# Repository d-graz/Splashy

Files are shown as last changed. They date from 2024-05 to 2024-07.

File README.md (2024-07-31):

# Splashy
<p align="center">
  
</p>

*"Splashy is a penguin shaped robot that helps you in refilling your water bottle"*
- Politecnico di Milan, Robotics \& Design course, A.Y. 2023/2024

<div align="center">
  <video src="https://github.com/user-attachments/assets/b8be0e26-66e1-40f9-9cfe-064658929ba2" width="1280" />
</div>

### Table of content
- [Introduction](#introduction)
- [Do It Yourself](#diy)
- [Credits](#credits)

## Introduction
This project started with the task *to create something that would have changed the behavior of people* (for the better of course =) ) on campus, given the constrain of non-mobility of such robot. Given such a constrain we explored some ideas before realizing that plastic has been a problem since forever and that the water refillers on campus where not that good. In fact thoose machines were slow resulting in a booring queue during peak hours. This somethimes would result in people buying  plastic water bottles from vending machines.\
Now i will **briefly** present some design challenges encoutered during developing of such a project. The full report can be found [here](documentation/report.pdf)

### How to attract people the first time (discovery)
The robot embeds a `PIR Sensor` able to detect motion. If the robot is not current under usage it will attract people passing by using it's wings (`servo motors` handles motion) and adjusting it's facial expression(rendered using `8x8 led matrices`).

### How to attract people in the long run (re-usage)
Splashy has a `NFC Reader`. This nfc can be used to identify users and thus create a rank based on the quantity of recharges that have been made. The rank is presented using an `LCD Screen`. This creates a gamification aspect in the refilling process

### Distribution of water
The water can be pumped from a water tank using a `pump` (like in our case) or alternative the penguin can be directly attached to a pressured faucet by replacing the pump with a `electric driven valve` 

## DIY
If you plan to recreate this project:
1. find all the components used for Splasy [here](documentation/BOM.pdf)
2. find all the 3d-printable in the `stl` directory
3. give a **careful** read to the [report](documentation/report.pdf)
4. Additionally read [user manual](documentation/user_manual.pdf) and [maintence manual](documentation/maintence_manual.pdf)

## Credits
<p align="center">
  
</p>

From left to rigth:
- Gianluca Miglietta (Automation Engineer)
- Davide Grazzani    (me, Computer Science Engineer)
- Sofia Maria Ciccia (School of Design and Engineering)
- Enrico Virgili     (School of Design and Engineering)

Supervisors:
- prof. Andrea Bonarini
- prof. Maximiliano Ernesto Romero

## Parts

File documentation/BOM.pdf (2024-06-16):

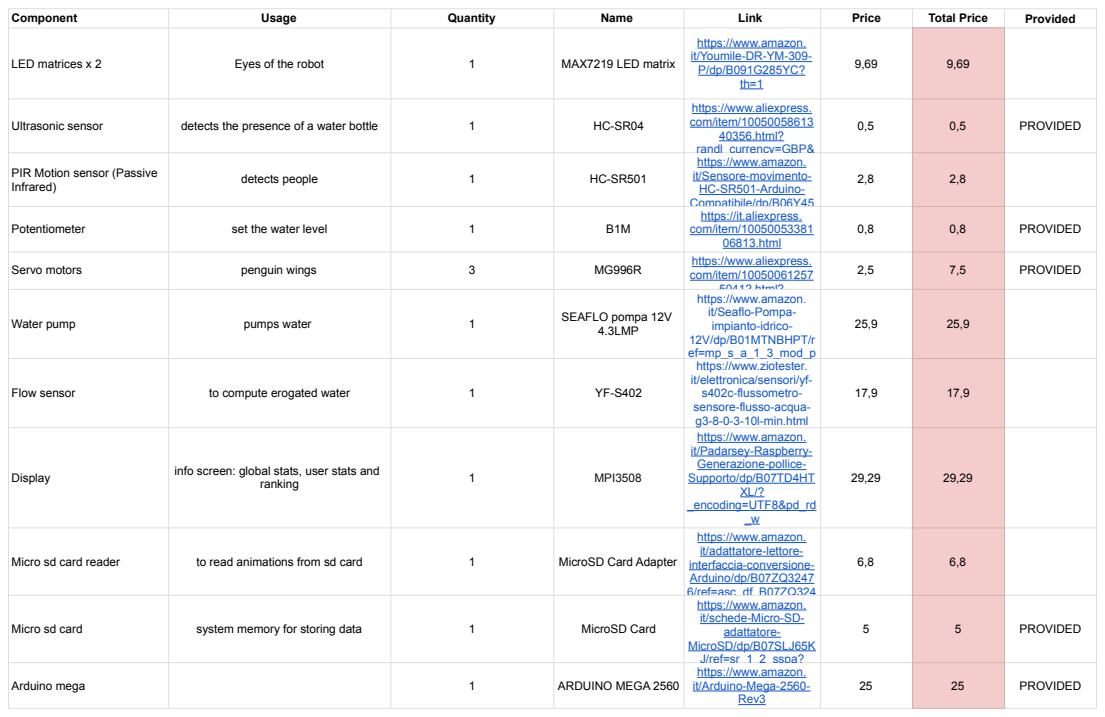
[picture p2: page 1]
Component; Usage; Quantity; Name; Link; Price; Total Price; Provided; LED matrices x 2; Eyes of the robot; MAX7219 LED matrix; Ultrasonic sensor; detects the presence of a water bottle; PROVIDED; Infrared); detects people; Potentiometer; set the water level; Servo motors; penguin wings; Water pump; pumps water; SEAFLO pompa 12V 4.3LMP; Flow sensor; to compute erogated water; Display; info screen: global stats, user stats and; ranking; MPI3508; Micro sd card reader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

https://www.amazon.
it/Youmile-DR-YM-309-

https://www.aliexpress.
com/item/10050058613
40356.html?
_randl_currency=GBP& (https://www.aliexpress.com/item/1005005861340356.html?_randl_currency=GBP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)
it/Sensore-movimento-
HC-SR501-Arduino-
Compatibile/dp/B06Y45 (https://www.amazon.it/Sensore-movimento-HC-SR501-Arduino-Compatibile/dp/B06Y459ZZK)
https://it.aliexpress.
com/item/10050053381
06813.html (https://it.aliexpress.com/item/1005005338106813.html?src=google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)
com/item/10050061257 (https://www.aliexpress.com/item/1005006125750412.html?src=google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)
50412.html?
it/Seaflo-Pompa-
impianto-idrico-
12V/dp/B01MTNBHPT/r
ef=mp_s_a_1_3_mod_p (https://www.amazon.it/Seaflo-Pompa-impianto-idrico-12V/dp/B01MTNBHPT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)
https://www.ziotester.
it/elettronica/sensori/yf-
s402c-flussometro-
sensore-flusso-acqua-
g3-8-0-3-10l-min.html (https://www.ziotester.it/elettronica/sensori/yf-s402c-flussometro-sensore-flusso-acqua-g3-8-0-3-10l-min.html)

PIR Motion sensor (Passive

https://www.amazon.it/Padarsey-Raspberry-Generazione-pollice-Supporto/dp/B07TD4HT 29,29 XL/? _encoding=UTF8&pd_rd _w (https://www.amazon.it/Padarsey-Raspberry-Generazione-pollice-Supporto/dp/B07TD4HTXL/) | 29,29

https://www.amazon.it/adattatore-lettore-interfaccia-conversione-6,8Arduino/dp/B07ZQ32476/ref=asc_df_B07ZQ324 (https://www.amazon.it/adattatore-lettore-interfaccia-conversione-Arduino/dp/B07ZQ32476?hvadid=655703548252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) https://www.amazon.it/schede-Micro-SD-adattatore-5MicroSD/dp/B07SLJ65KJ/ref=sr_1_2_sspa? (https://www.amazon.it/schede-Micro-SD-adattatore-MicroSD/dp/B07SLJ65KJ?sp_csd=d2lkZ2V0TmFtZT1zcF9hdGY) https://www.amazon.it/Arduino-Mega-2560-25 Rev3 (https://www.amazon.it/Arduino-Mega-2560-Rev3-microcontrollore/dp/B0046AMGW0?hvadid=194963093038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) | | 6,8 5 25 | PROVIDED

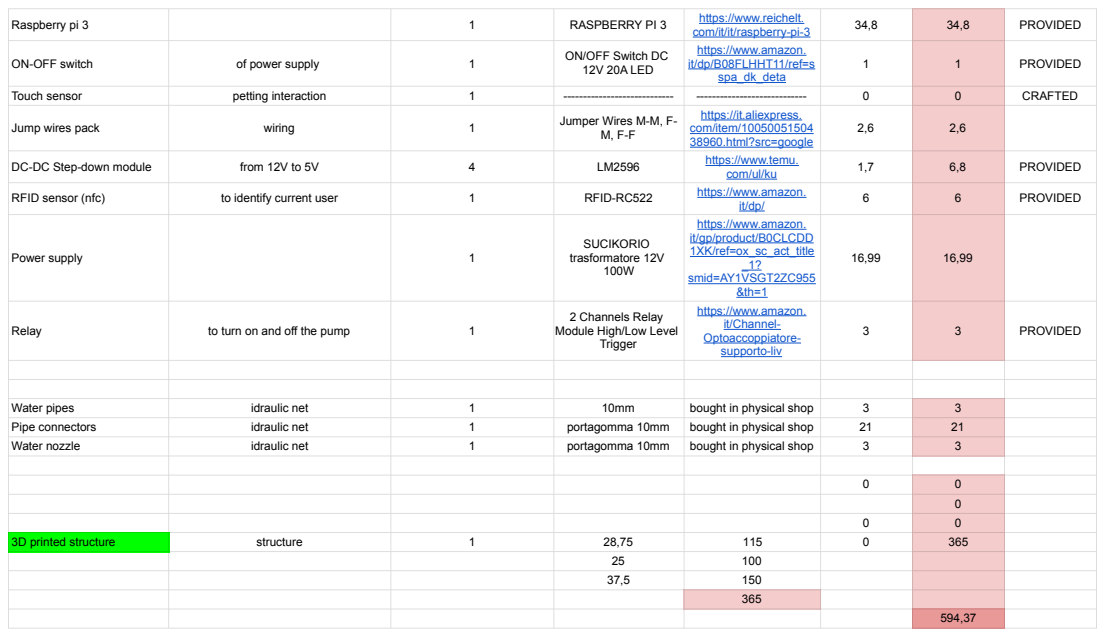
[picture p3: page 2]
Raspberry pi 3; RASPBERRY PI 3; https://www.reichelt.; com/it/it/raspberry-pi-3; PROVIDED; ON-OFF switch; of power supply; ON/OFF Switch DC; 12V 20A LED; Touch sensor; petting interaction; CRAFTED; Jump wires pack; wiring; Jumper Wires M-M, F- M, F-F; DC-DC Step-down module; from 12V to 5V; https://www.temu.; com/ul/ku; RFID sensor (nfc); to identify current user; RFID-RC522; https://www.amazon.; Power supply; SUCIKORIO trasformatore 12V 100W; _1? smid=AY1VSGT2ZC955 &th=1; Relay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

https://www.amazon.
it/dp/B08FLHHT11/ref=s
spa_dk_deta (https://www.amazon.it/dp/B08FLHHT11?s=industrial&sp_csd=d2lkZ2V0TmFtZT1zcF9kZXRhaWw)

https://it.aliexpress.
com/item/10050051504
38960.html?src=google (https://it.aliexpress.com/item/1005005150438960.html?src=google)

it/gp/product/B0CLCDD
1XK/ref=ox_sc_act_title

it/Channel-
Optoaccoppiatore-
supporto-liv (https://www.amazon.it/Channel-Optoaccoppiatore-supporto-livello-attivazione/dp/B07QLX1YZN)

2 Channels Relay
Module High/Low Level

3D printed structure | structure 1 28,75 115 0 | 365

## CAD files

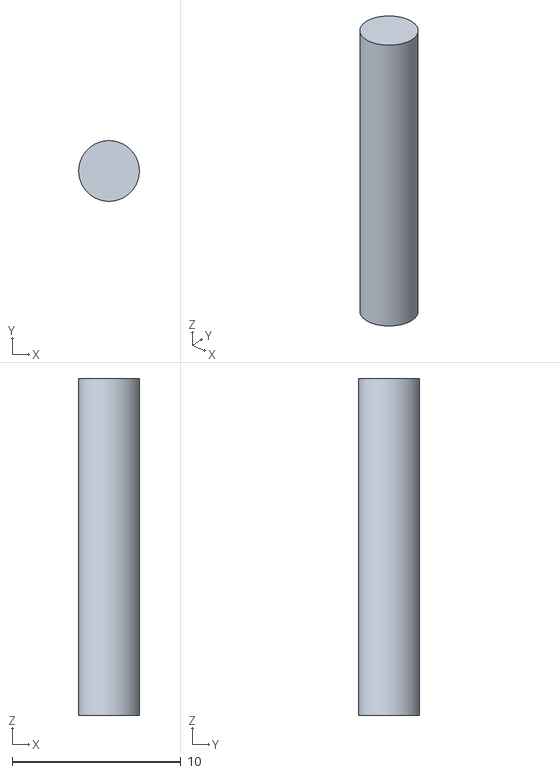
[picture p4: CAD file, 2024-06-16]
stl/wing_center_joint_x2.STL
3.60 x 3.60 x 20.0

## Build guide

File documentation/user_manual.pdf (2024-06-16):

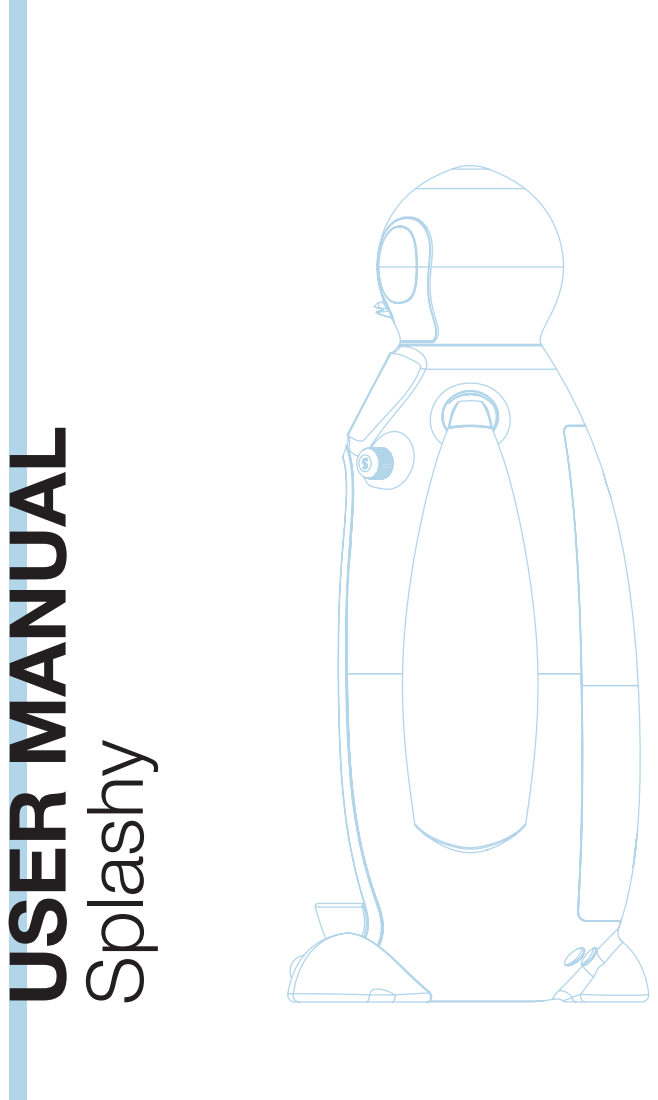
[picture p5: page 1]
pla

# DESIGN&ROBOTICS

## Professors:

## Andrea Bonarini, Maximiliano Romero

## Tutors:

## Federico Espositi

## Group 3

## Sofia Maria Ciccia Davide Grazzani Gianluca Miglietta Enrico Virgili

## 12° edition, 2024

# INDEX

1234

## introduction

## how to start

## how to use

## emotions

# 1introduction

## who is Splashy?

Splashy: Refill your Water Bottle,

## Refresh the Planet!

Splashy is an innovative water dispenser,

designed to be usable by anyone in many contexts, but with a strong sustainable objective. The idea of Splashy was born from the need to change an incorrect and harmful behavior for the environment: the continuous use of plastic bottles. This behavior contributes significantly to our planet's CO2 footprint. Splashy wants to encourage you to constantly use the water bottle, thus performing a positive action for the environment, making the experience

more engaging and pleasant than usual.

## Thanks to its intuitive and attractive interface, its attractive design and integrated gamification elements, Splashy incentivizes you to come back and use the service. Automatic and super-fast refilling of your water bottle makes Splashy not only a sustainable option, but also

convenient and fun.

## head

## LED screen

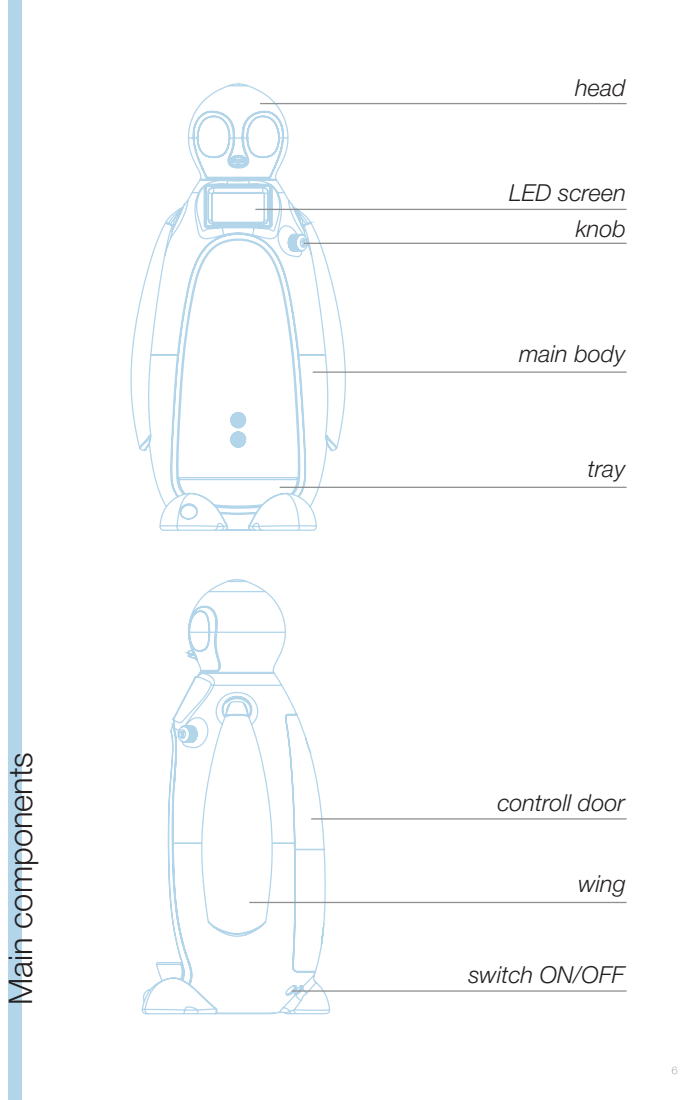
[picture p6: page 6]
Main components; knob; main body; tray; controll door; wing

switch ON/OFF

# 2how to start

1
2

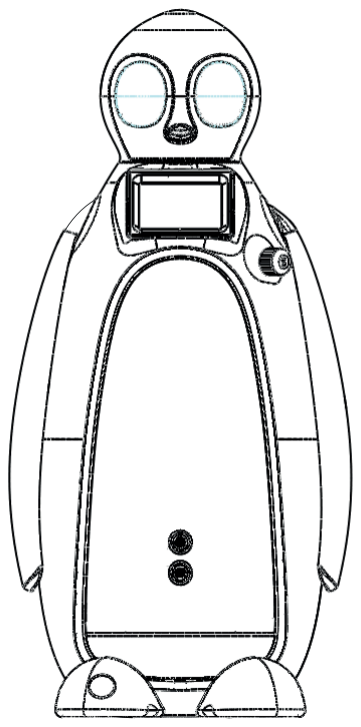
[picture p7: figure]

1

Take from the box Splashy. The robot doesn’t need any kind of assembly. You can start to use immediately!
Place the robot on a stable surface.

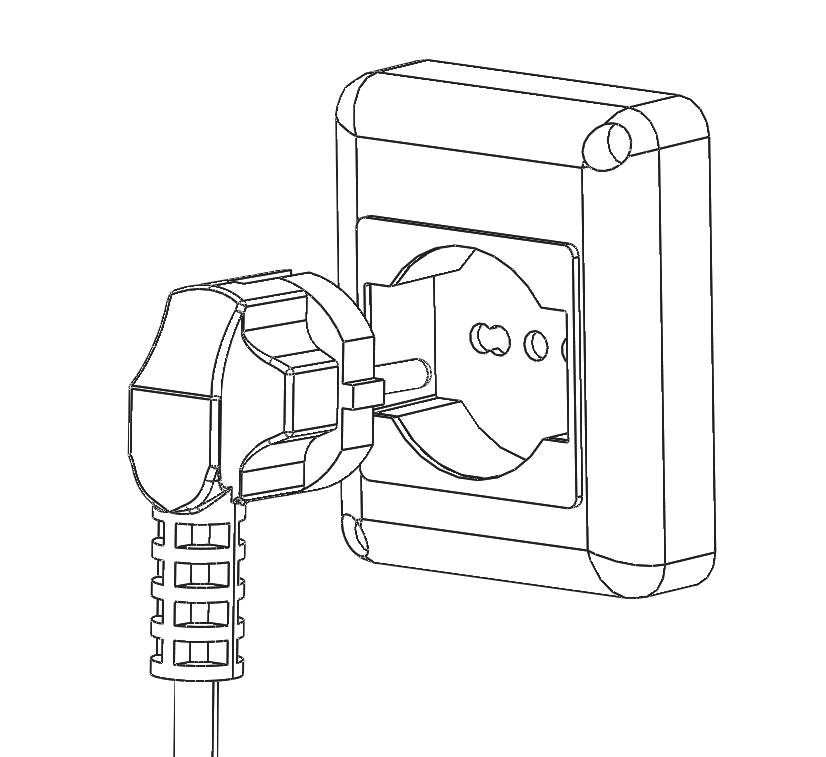
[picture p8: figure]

2

Plug the Schuko cable into the electric socket.

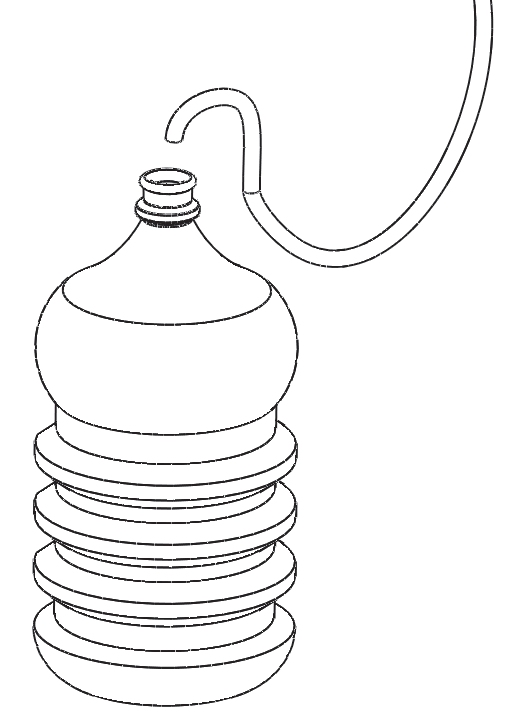
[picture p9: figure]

3

Put the water pipe into the gallon.

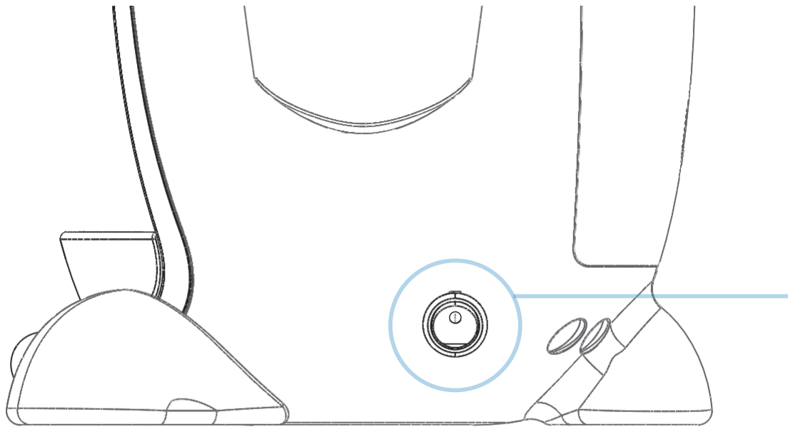
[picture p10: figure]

4

Turn on the robot from the switch

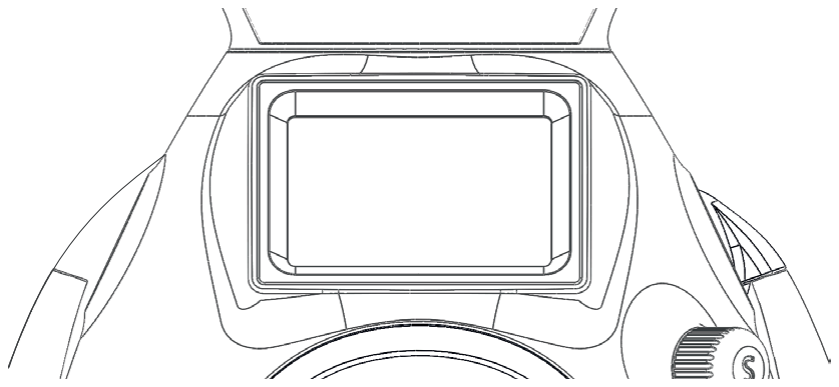
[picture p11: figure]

5

Wait until the screen shows the ranking

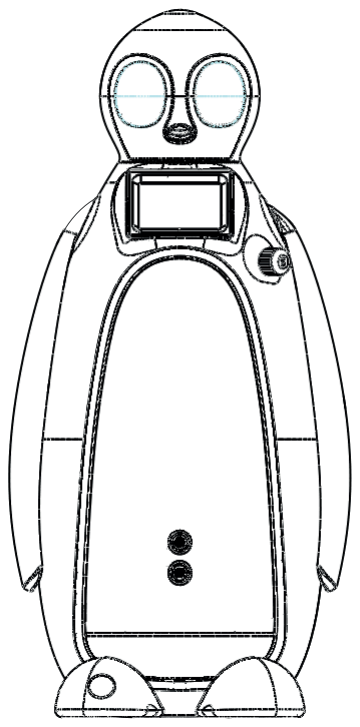
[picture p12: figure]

6

Now you can freely use the robot!

# 3how to use

2

1

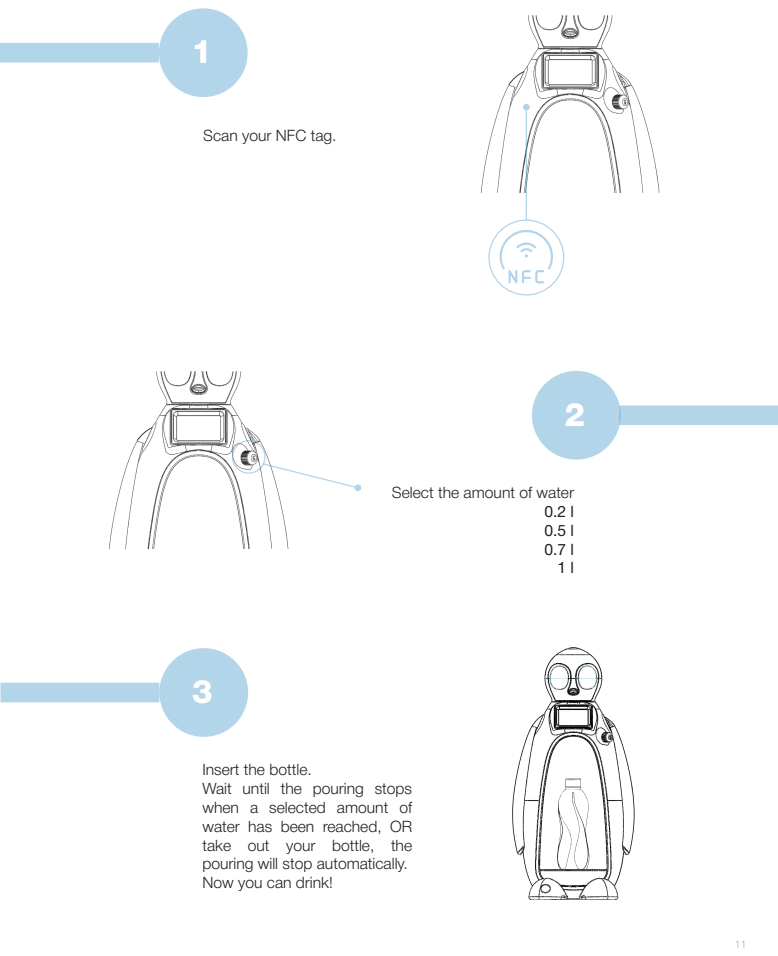
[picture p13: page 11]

Scan your NFC tag.

Select the amount of water

Insert the bottle.
Wait until the pouring stops
when a selected amount of
water has been reached, OR
take out your bottle, the
pouring will stop automatically.
Now you can drink!

2

# 4emotions

1

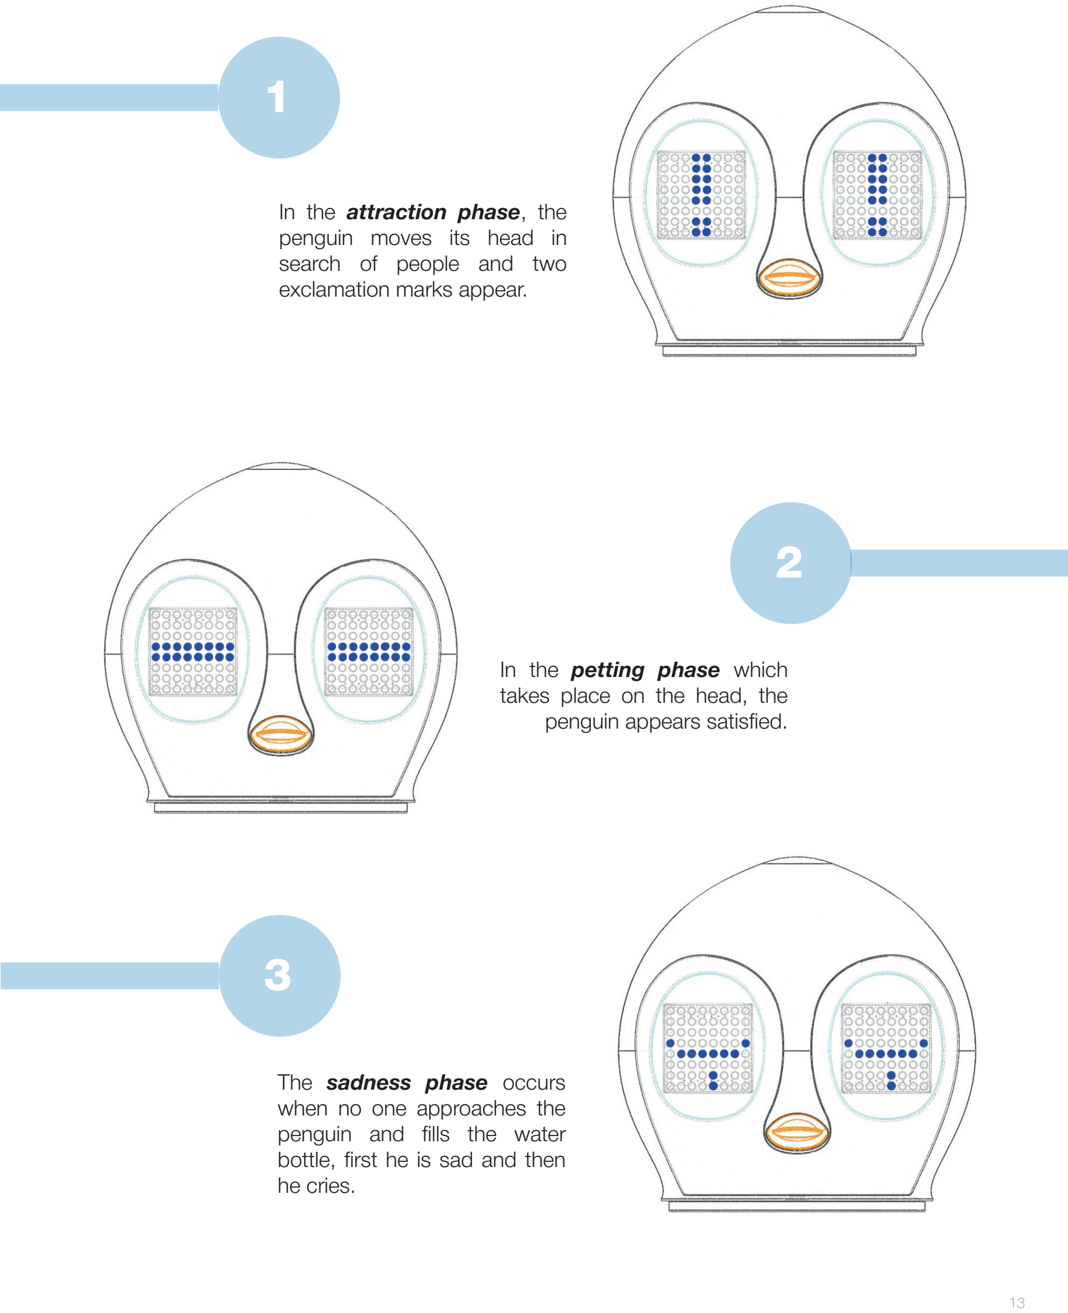
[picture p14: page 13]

In the attraction phase, the penguin moves its head in
search of people and two
exclamation marks appear.

2

In the petting phase which takes place on the head, the penguin appears satisfied.

3

The sadness phase occurs
when no one approaches the penguin and fills the water bottle, first he is sad and then he cries.

3

4

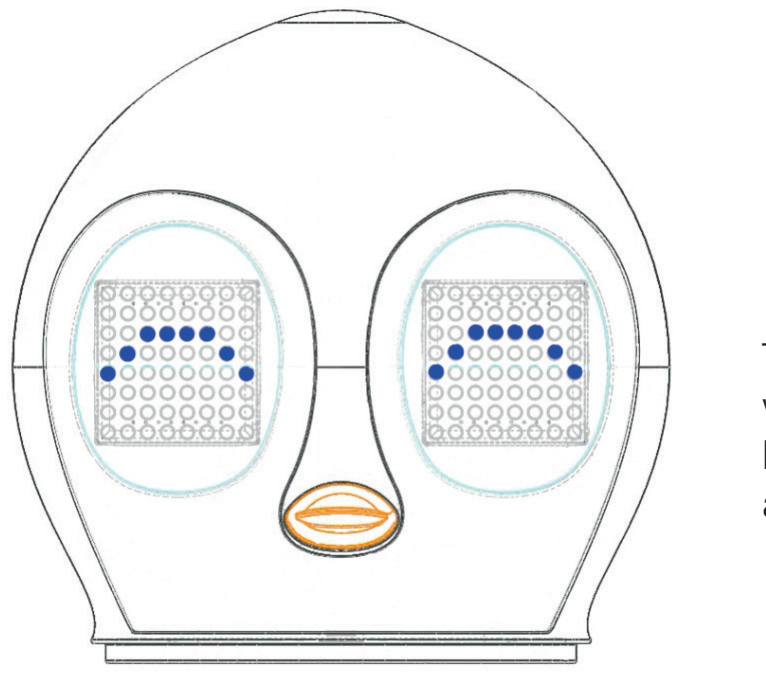
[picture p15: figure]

The happiness phase occurs when someone fills the water
bottle, | when | someone
approaches and after every 5
| | bottles filled

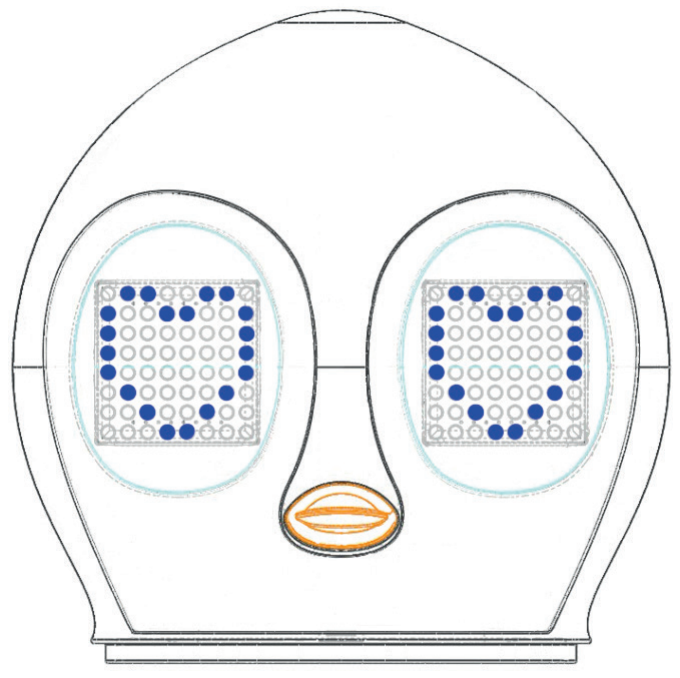
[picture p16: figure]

5

During the water refill phase, the eyes become two hearts that fill gradually, until they are completely full when they flash and it is possible to remove the bottle

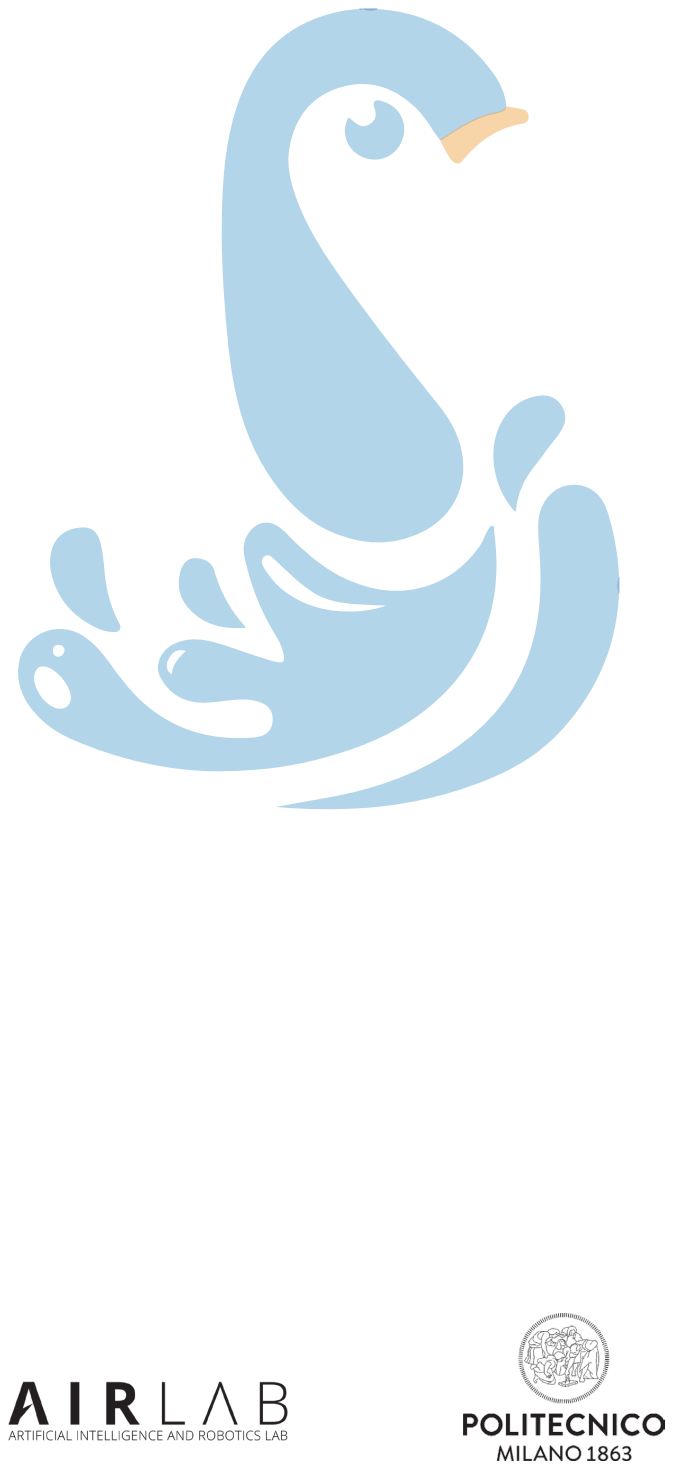
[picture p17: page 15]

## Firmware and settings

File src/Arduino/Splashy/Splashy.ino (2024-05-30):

// ####################### LIBRARIES ###########################
// release libraries
#include "libraries/Config/Config.hpp"


//#define DEBUG
//#define WARN
//#define TEST 
// debug libraries
#include "libraries/LedMatrix/LedMatrix.hpp"
#include "libraries/LedMatrix/LedMatrix.cpp"
#include "libraries/MySD/MySD.hpp"
#include "libraries/MySD/MySD.cpp"
#include "libraries/TaskManagement/TaskManagement.hpp"
#include "libraries/TaskManagement/TaskManagement.cpp"
#include "libraries/ServoController/ServoController.hpp"
#include "libraries/ServoController/ServoController.cpp"
#include "libraries/UltrasonicSensor/UltrasonicSensor.hpp"
#include "libraries/UltrasonicSensor/UltrasonicSensor.cpp"
#include "libraries/ProximitySensor/ProximitySensor.hpp"
#include "libraries/ProximitySensor/ProximitySensor.cpp"
#include "libraries/FiniteStateMachine/FiniteStateMachine.hpp"
#include "libraries/FiniteStateMachine/FiniteStateMachine.cpp"
#include "libraries/Pump/Pump.hpp"
#include "libraries/Pump/Pump.cpp"
#include "libraries/TouchSensor/TouchSensor.hpp"
#include "libraries/TouchSensor/TouchSensor.cpp"
#include "libraries/Config/Global.hpp"
#include "libraries/Core/Core.hpp"
#include "libraries/Core/Core.cpp"


// ######################## DEFINE #############################
#define BAUD_RATE 9600

// ##################### GLOBAL VARS ###########################
// scheduler
Scheduler *scheduler;

// fsm
FiniteStateMachine *fsm;


// ##################### SETUP #################################
void setup() {
  // start serial communication
  Serial.begin(BAUD_RATE);
  delay(2000);
  #ifdef DEBUG
    Serial.println(F("Init setup"));
    #ifdef TEST
      delay(1000);
    #endif
  #endif

  //init the scheduler
  scheduler = new Scheduler();

  //init the led matrix early to enable error handling
  #ifdef DEBUG
    Serial.println(F("Init LedMatrix"));
  #endif
  led_matrix = new LedMatrix("Led");
  handle_error(scheduler->add_task(led_matrix), F("Failed to add LedMatrix to the scheduler"));

  //init the sd card early to load boot animation
  #ifdef DEBUG
    #ifdef TEST
      delay(1000);
    #endif
    Serial.println(F("Init SD card"));
  #endif
  handle_error(init_sd(), F("Failed to initialize SD card"));

  //load the boot animation
  #ifdef DEBUG
    #ifdef TEST
      delay(1000);
    #endif
    Serial.println(F("Loading boot animation"));
  #endif
  handle_error(led_matrix->load_animation(LedMatrixAnimation::Boot), F("Failed to load boot animation"));
  handle_error(scheduler->executeByName(F("Led"), 3), F("Failed to execute LedMatrix"));

  //init the servo controller
  #ifdef DEBUG
    #ifdef TEST
      delay(1000);
    #endif
    Serial.println(F("Init ServoController, adding to the scehduler and homing the servo"));
  #endif
  servo_controller = new ServoController("Servo");
  handle_error(scheduler->add_task(servo_controller), F("Failed to add ServoController to the scheduler"));
  handle_error(scheduler->executeByName(F("Led")), F("Failed to execute LedMatrix"));
  servo_controller->home(true);
  handle_error(scheduler->executeByName(F("Led"), 3), F("Failed to execute LedMatrix"));

  //testing servo motors if test
  #ifdef DEBUG
    #ifdef TEST
      Serial.println(F("Testing servo motors"));
      handle_error(servo_controller->load_animation(ServoMotorAnimation::Test), F("Failed to load test animation for servocontroller"));
      while(servo_controller->get_status() != TaskStatus::HIBERNATED){
        handle_error(scheduler->executeAll(), F("Failed to execute the scheduler"));
      }
      Serial.println(F("Test done"));
      Serial.println(F("Continuing the boot process"));
    #endif
  #endif

  //init the ultrasonic sensor
  #ifdef DEBUG
    #ifdef TEST
      delay(1000);
    #endif
    Serial.println(F("Init UltrasonicSensor and adding to the scheduler"));
  #endif
  ultrasonic_sensor = new UltrasonicSensor("Usonic");
  handle_error(scheduler->executeByName(F("Led")), F("Failed to execute LedMatrix"));
  handle_error(scheduler->add_task(ultrasonic_sensor), F("Failed to add UltrasonicSensor to the scheduler"));
  handle_error(scheduler->executeByName(F("Led"), 3), F("Failed to execute LedMatrix"));

  //init the proximity sensor
  #ifdef DEBUG
    #ifdef TEST
      delay(1000);
    #endif
    Serial.println(F("Init ProximitySensor and adding to the scheduler"));
  #endif
  proximity_sensor = new ProximitySensor("Prox");
  handle_error(scheduler->executeByName(F("Led")), F("Failed to execute LedMatrix"));
  handle_error(scheduler->add_task(proximity_sensor), F("Failed to add ProximitySensor to the scheduler"));
  handle_error(scheduler->executeByName(F("Led"), 3), F("Failed to execute LedMatrix"));

  //init the pump
  #ifdef DEBUG
    #ifdef TEST
      delay(1000);
    #endif
    Serial.println(F("Init Pump and adding to the scheduler"));
  #endif
  pump = new Pump("Pump");
  handle_error(scheduler->executeByName(F("Led")), F("Failed to execute LedMatrix"));
  handle_error(scheduler->add_task(pump), F("Failed to add Pump to the scheduler"));
  handle_error(scheduler->executeByName(F("Led")), F("Failed to execute LedMatrix"));

  //init the touch sensor
  #ifdef DEBUG
    #ifdef TEST
      delay(1000);
    #endif
    Serial.println(F("Init TouchSensor and adding to the scheduler"));
  #endif
  touch_sensor = new TouchSensor("Touch");
  //handle_error(scheduler->executeByName(F("Led")), F("Failed to execute LedMatrix"));
  //handle_error(scheduler->add_task(touch_sensor), F("Failed to add TouchSensor to the scheduler"));
  //handle_error(scheduler->executeByName(F("Led"), 3), F("Failed to execute LedMatrix"));

  //init the fsm
  #ifdef DEBUG
    #ifdef TEST
      delay(1000);
    #endif
    Serial.println(F("Init FiniteStateMachine"));
  #endif
  fsm = new FiniteStateMachine();
  handle_error(scheduler->executeByName(F("Led"), 2), F("Failed to execute LedMatrix"));

  // activating proximity sensor, ultrasonic sensor and proximity before entering the loop in IDLE status
  #ifdef DEBUG
    #ifdef TEST
      delay(1000);
    #endif
    Serial.println(F("Activating proximity sensor and ultrasonic sensor before entering the loop in IDLE status"));
  #endif
  handle_error(proximity_sensor->activate(), F("Failed to activate proximity sensor"));
  handle_error(ultrasonic_sensor->activate(), F("Failed to activate ultrasonic sensor"));
  handle_error(touch_sensor->activate(), F("Failed to activate touch sensor"));
  handle_error(scheduler->executeByName(F("Led"), 3), F("Failed to execute LedMatrix"));

  //load the idle animation facial expression
  handle_error(led_matrix->load_animation(LedMatrixAnimation::Idle), F("Failed to load idle animation"));

  #ifdef DEBUG
    Serial.println(F("Setup done"));
    #ifdef TEST
      delay(1000);
    #endif
  #endif

}


// ######################## LOOP ###############################
void loop() {
  // execute the fsm
  #ifdef DEBUG
    #ifdef WARN
      Serial.println(F("Executing the FSM"));
    #endif
  #endif
  fsm->next();

  // execute the scheduler
  #ifdef DEBUG
    #ifdef WARN
      Serial.println(F("Executing the scheduler"));
    #endif
  #endif
  handle_error(scheduler->executeAll(), F("Failed to execute the scheduler"));

  delay(5);

  #ifdef DEBUG
    #ifdef TEST
      delay(5000);
    #endif
  #endif

}

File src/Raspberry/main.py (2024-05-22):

from DatabaseConnectionManager import DatabaseConnectionManager
from NFCReader import RFIDReader
from SerialManager import SerialManager
from PySide2 import QtWidgets
from GUI import Ui_MainWindowSplashy
import sys
import time

if __name__ == "__main__":

    # wait 5 seconds at startup
    time.sleep(5)

    # set up the database connection
    db = DatabaseConnectionManager()

    # set up the nfc module and start reading
    nfc = RFIDReader()
    nfc.start_reading()

    # set up the serial communication with Arduino and start reading
    serial = SerialManager(db, nfc)
    serial.start_reading()

    # set up the GUI
    app = QtWidgets.QApplication(sys.argv)
    MainWindowSplashy = QtWidgets.QMainWindow()
    ui = Ui_MainWindowSplashy()
    ui.setupUi(MainWindowSplashy, db, nfc)

    # start the cleanup thread for the database
    db.start_clean_up_thread()

    # start the GUI
    MainWindowSplashy.show()

    # run the application
    sys.exit(app.exec_())

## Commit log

2024-03-14 Started working on animation class for the matrix led
2024-03-15 Version 1.0 of animation library ready + sample of animation
2024-03-18 Added non compiling arduino class for handling led matricies
2024-03-19 Fixed compiling issue + add some new animation, test of card module and LedMatrix needed
    [Splashy.ino]
2024-03-22 Fix to read file for LedMatrix animation
2024-03-22 Major changes on LedMatrix lib that now supports threading thanks to TaskClass (added, not complete) + update of sim environment
2024-03-27 Major changes across the board
2024-03-29 Major changes to ServoController library including non-blocking call to write() function
2024-03-30 Major changes across the board, including changes to static scheduler memory management
2024-04-01 Added ProximitySensor class for handling ultrasonic sensor
2024-04-05 Added new pump class
2024-04-05 Minor changes across the board and added new way to load animation on servocontroller class
2024-04-08 Added incomplete SerialManager class for intercepting messages from Arduino
2024-04-09 Major code refactor + added Proximity and pump simulation settings
2024-04-10 Fixed important bug in the scheduler that causes task scheduling failure
    [Splashy.ino]
2024-04-19 Added fixed Raspberry code, gui not present
    [DatabaseConnectionManager.py, NFCReader.py, SerialManager.py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]
2024-04-20 Added touch sensor, needs docs and test
2024-04-24 Fixup to UltrasonicSensor class which was not able to perform multiple subsequent pings without a delay
2024-04-24 Fixup to Pump that was not able to correctly attach to interrupt pin in order to monitor water flow
2024-04-24 Added new filter for Touch sensor
2024-05-19 Added some hardware test (arduino)
2024-05-19 Major bug fix on Raspberry codebase
    [DatabaseConnectionManager.py, GUI.py, NFCReader.py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]
2024-05-22 Added new state that wait some time for the user before starting the chargin process + continuos potentiometer reading
2024-05-22 Major gui bugfix + added file to delete databse
    [GUI.py]
2024-05-22 Added autostart at boot for raspberry gui
2024-05-23 Last changes to GUI and new timer for autostart application at boot on the raspberry
2024-05-30 Disabled touch sensor
2024-06-16 Minor changes + added BOM, user manual and maintance manual
2024-06-16 Added stl files
    [wing_center_joint_x2.STL]
